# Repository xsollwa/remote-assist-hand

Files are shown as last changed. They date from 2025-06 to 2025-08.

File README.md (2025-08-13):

# remote-assist-hand
A robotic hand with pressure sensing and haptic feedback communication

**Created by:** Ruzanna Gaboyan and Philip Golczak  
**Date:** May 28, 2025  
**Demo:** https://youtu.be/ImFqXYvcVdE

## Overview
The **Remote Assist Hand** is a robotic arm with a gripping hand that is able to sense how much pressure it feels when gripping and holding objects. It uses a load cell to measure this force and sends that information to a computer through an ESP32 microcontroller. Unlike most robotic arms, **Remote Assist Hand** can *sense physical resistance and communicate it back* to the user, which helps them to know how hard the robot is gripping without directly touching anything. 

**Why we made it:** By this project we wanted to learn more about haptic feedback and *communicating the "feeling of touch"* while controlling robots. This is especially helpful for tasks that demand percision when it comes to pressure awareness: like when handling delicate objects.

## Features
- **Force sensing with load cell:** Senses how much pressure the hand feels when it grabs an object.
- **Real time feedback to computer**: ESP32 wirelessly sends data from the hand to a computer.
- **Remote control using computer**: The arm is designed to be operated remotely through a computer. 
- **Custom PCB and 3D design**: All parts including the base, casing and PCB are custom designed and printed

### Materials and Budget

| Part Number | Part Name | Description | Unit Price | Total Price |
| :--- | :---: | :---: | :---: | ---: |
| MP1 | ESP32 | [Wi-Fi Microprocessor][1] | $10 | $10 |
| B1 | Urgenex Lipo Battery (2x) | [Battery for Arm and Remote][2] | $27 | $27 |
| M1 | Digital Servo Motor (4x) | [Servos for Joints][3] | $45 | $45 |
| M2 | Stepper Motor | [Stepper for Base][4] | $13 | $13 |
| L1 | Load Cell | [Load Cell for Grasper][5] | $12 | $12 |
| A1 | Amplifier (4x) | [Amplifier for Load Cell][6] | $7 | $7 |
| D1 | Stepper Driver (3x) | [Driver for Stepper][7] | $8 | $8 |
| C1 | Hex Coupler 5mm (4x) | [Hex Coupler for Base][8] | $8 | $8 |
| T1 | Threaded Inserts 4mm (100x) | [Threaded Inserts for Arm][9] | $10 | $10 |
| BC1 | Buck Converter 4mm (2x) | [Buck Converter for 7.4-5v][10] | $8 | $8 |
| L1 | 5v Voltage Regulator | [Voltage Regulator for ESP32][11] | NA(Owned)  | NA(Owned) |
| PCB1 | Printed Circuit Board | [PCB for Electrical Components][12] | ~$10 | ~$10 |
| S1 | Boat Rocker Switch | [Power Switch][13] | $5 | $5 |
| TOT | Total (Excluding taxes, shipping and fees) | | | $163 |

[1]: https://www.amazon.com/HiLetgo-ESP-WROOM-32-Development-Microcontroller-Integrated/dp/B0718T232Z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

[2]: https://www.amazon.com/URGENEX-Battery-1800mAh-Rechargeable-Campatibal/dp/B0924MM61Z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

[3]: https://www.amazon.com/HOOYIJ-Digital-Waterproof-Crawler-Control/dp/B0CJ79WBZ8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

[4]: https://www.amazon.com/Stepper-Motor-Bipolar-64oz-Printer/dp/B00PNEQI7W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

[5]: https://www.amazon.com/uxcell-Weighing-Electronic-Balance-Sensor/dp/B07NS81RT6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

[6]: https://www.amazon.com/WWZMDiB-HX711-Amplifier-Displacement-Acceleration/dp/B0BLND4VF6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

[7]: https://www.amazon.com/WWZMDiB-Stepstick-Stepper-Printer-Suitable/dp/B0BFQZWT6R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

[8]: https://www.amazon.com/uxcell-Coupler-Coupling-Connector-Wheels/dp/B08M379TCT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

[9]: https://www.amazon.com/HANGLIFE-Heat-Set-Threaded-Printing-Components/dp/B0CS6XGMFD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

[10]: https://www.amazon.com/Maxmoral-Converter-Adjustable-Step-Down-Regulator/dp/B07MKQXNWG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

[11]: https://www.amazon.com/BOJACK-Regulator-Integrated-Circuits-Regulators/dp/B07VRS9HW4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

[12]: https://cart.jlcpcb.com/quote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

[13]:https://www.amazon.com/10PCS-Rocker-Switch-Rectangle-Black/dp/B094FWYWL5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

### Notes on Purchasing and Shipping
We want to purchase most of the parts from Amazon. We chose Amazon as our primary supplier because we have access to Amazon Prime, which has faster and free shipping. The free shipping makes the packs cheaper than the singular alternatives at other sources. Some components, like the voltage regulators, were only available in multi packs, so the unit price listed is price of the whole pack. Also, we plan to use some of the parts, like the battery and voltage regulators, for our next project, so their cost is shared across multiple builds!

## How it Works
1) Servo motors (controlled from a computer) move the arm and the gripper to **hold an object**,
2) The load cell inside the gripper **measures how much force** is being applied,
3) ESP32 **sends the data to a computer** in real time,
4) The computer **displays the pressure**, helping the user understand how hard the robot is gripping.

## Pictures 

**Overview Wiring Diagram**

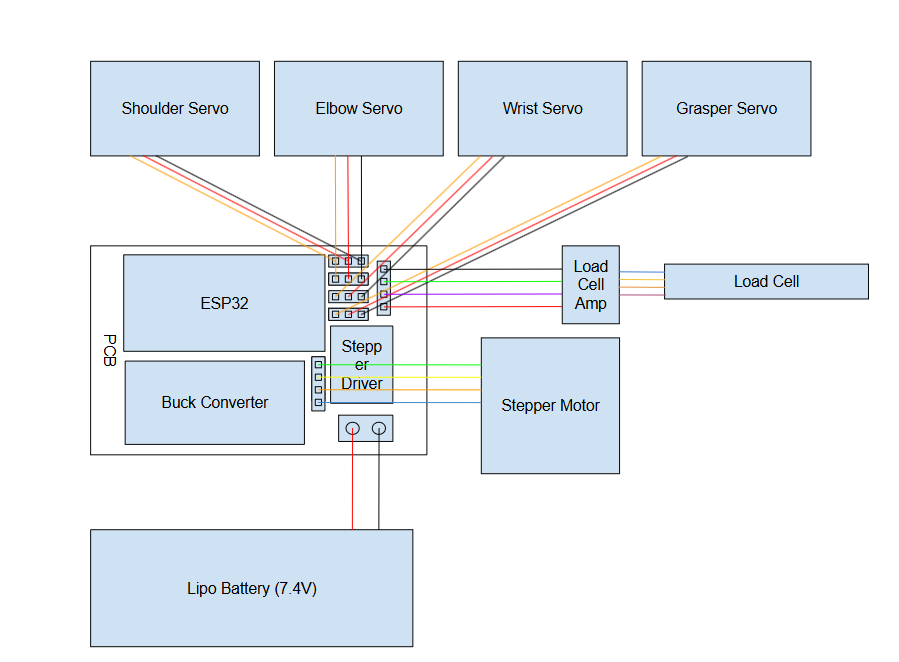
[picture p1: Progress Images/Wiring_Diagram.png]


**PCB**
Arm_Wiring_Final
PCB_Design

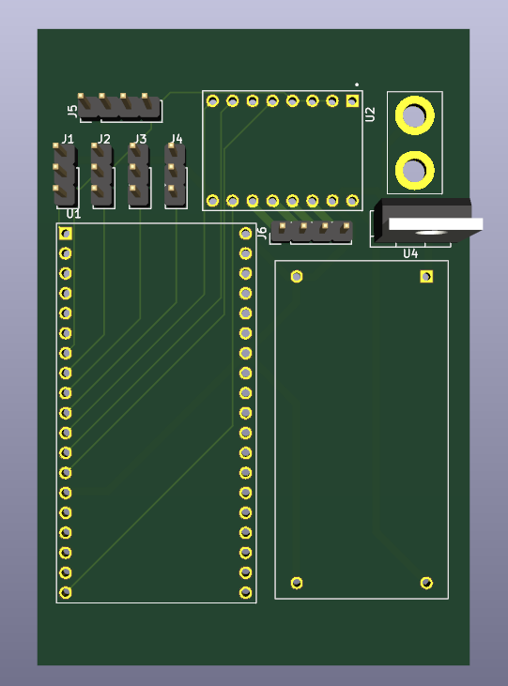
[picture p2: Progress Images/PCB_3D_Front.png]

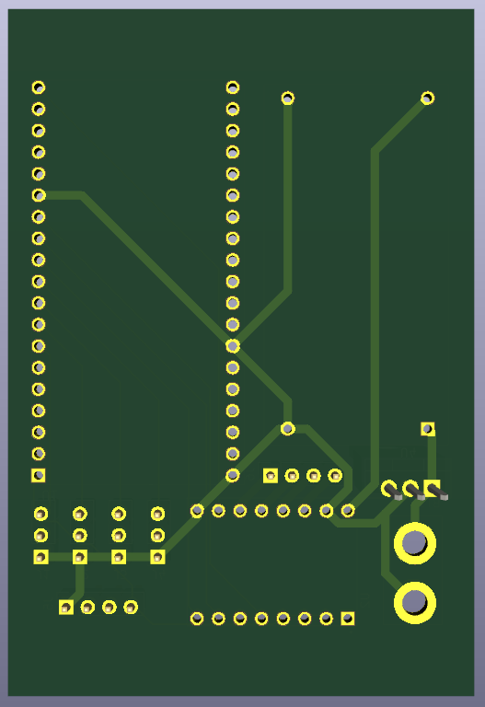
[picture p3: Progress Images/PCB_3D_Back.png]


**3D model**
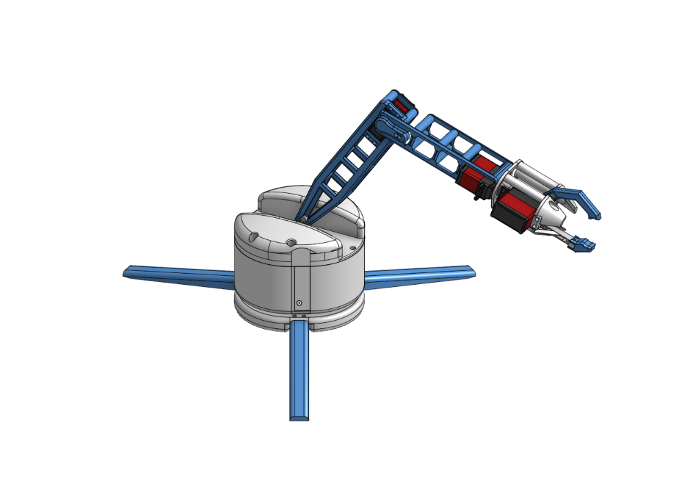
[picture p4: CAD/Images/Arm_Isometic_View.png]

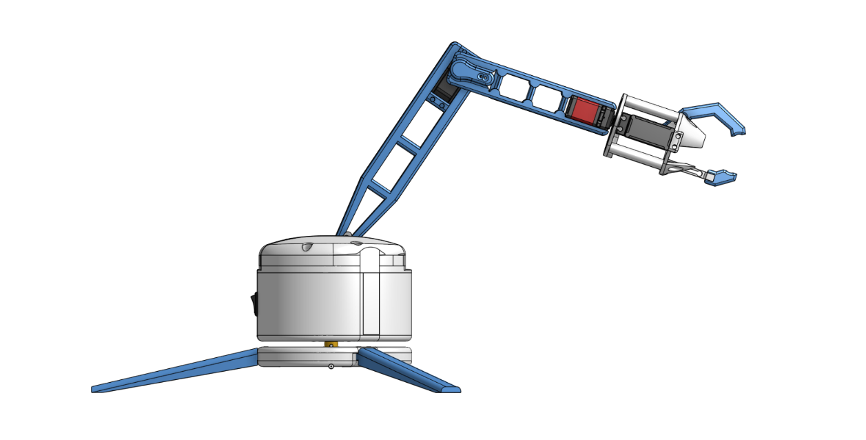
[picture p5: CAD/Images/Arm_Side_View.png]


**Build IRL**
Complete_Arm (1)

## Building Process
1) Brainstorming and sketching
2) PCB Design using KiCAD 
3) CAD Modeling using OnShape
4) Revision and Optimization
5) Assembly and testing

## Journal
Our full development journal can be found [here](./JOURNAL.md) (includes what we struggled with and what we learnt)

## Contact
For any questions or suggestions please reach out to us at *gaboyanruzanna@gmail.com* or *ph.golczak@gmail.com* .

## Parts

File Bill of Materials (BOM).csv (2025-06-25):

Part Number | Part Name | Description | Unit Price | Total Price
MP1 | ESP32 | Wi-Fi Microprocessor | $10 | $10
B1 | Urgenex Lipo Battery (2x) | Battery for Arm and Remote | $27 | $27
M1 | Digital Servo Motor (4x) | Servos for Joints | $45 | $45
M2 | Stepper Motor | Stepper for Base | $13 | $13
L1 | Load Cell | Load Cell for Grasper | $12 | $12
A1 | Amplifier (4x) | Amplifier for Load Cell | $7 | $7
D1 | Stepper Driver (3x) | Driver for Stepper | $8 | $8
C1 | Hex Coupler 5mm (4x) | Hex Coupler for Base | $8 | $8
T1 | Threaded Inserts 4mm (100x) | Threaded Inserts for Arm | $10 | $10
BC1 | Buck Converter 4mm (2x) | Buck Converter for 7.4-5v | $8 | $8
L1 | 5v Voltage Regulator | Voltage Regulator for ESP32 | NA(owned) | NA(owned)
PCB1 | Printed Circuit Board | PCB for Electrical Components | ~$10 | ~$10
S1 | Boat Rocker Switch | Power Switch | $5 | $5
Total (excluding taxes, shipping and fees): |  |  |  | $163

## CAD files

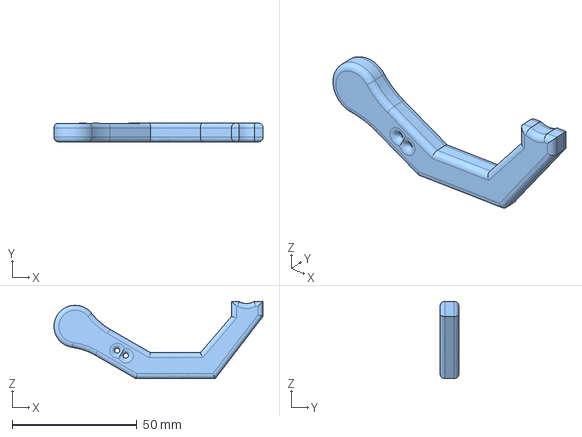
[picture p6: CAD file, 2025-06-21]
Production/Claw Top.step
83.9 x 7.50 x 31.0 mm

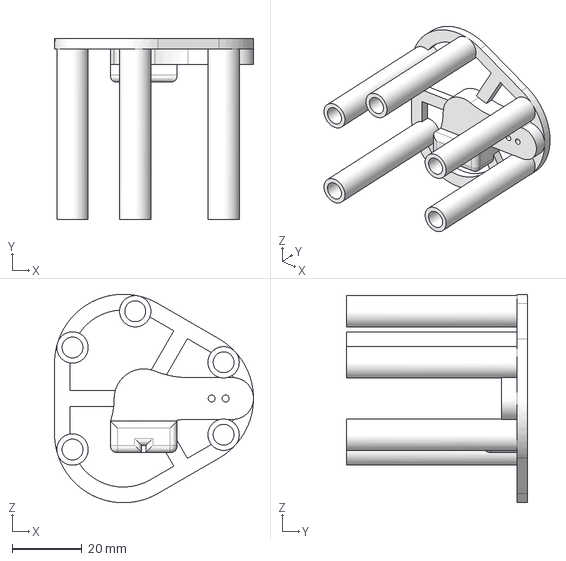
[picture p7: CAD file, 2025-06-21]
Production/Wrist Female.step
57.1 x 51.9 x 59.9 mm

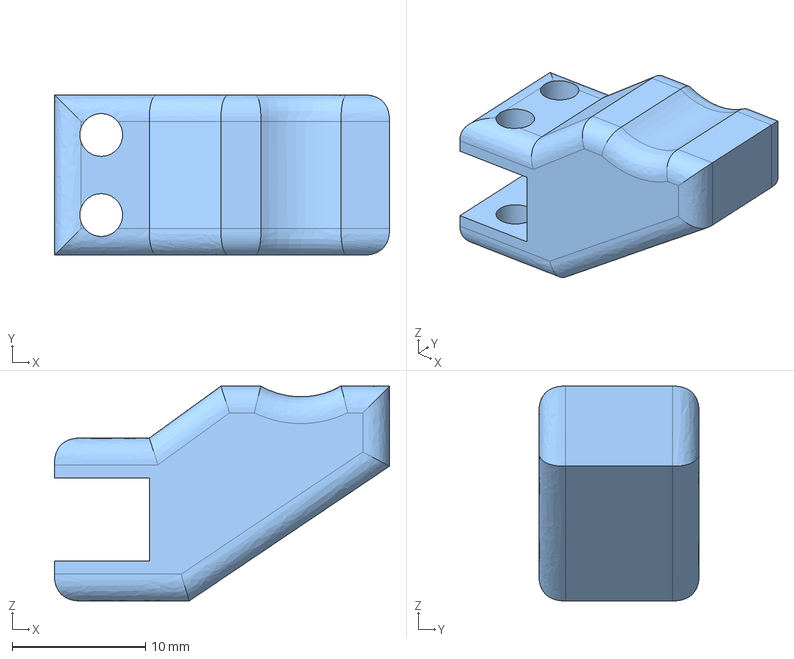
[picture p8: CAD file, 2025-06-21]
Production/Claw Bottom.step
25.1 x 12.0 x 16.1 mm

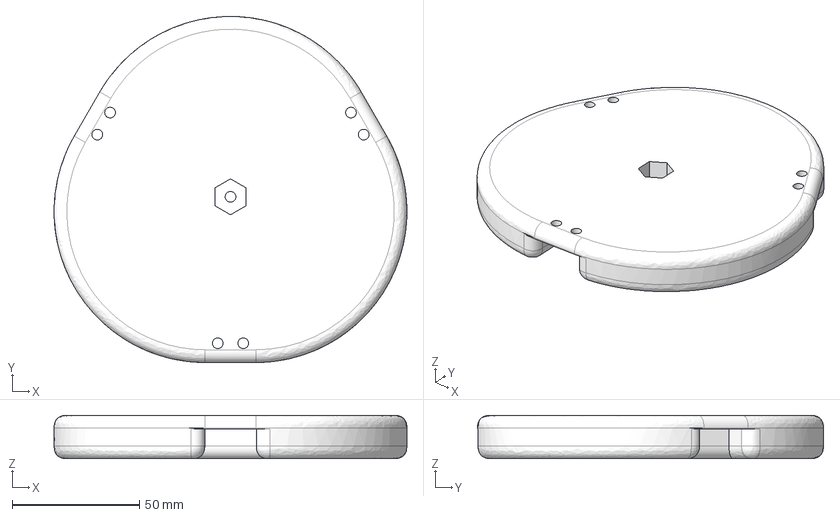
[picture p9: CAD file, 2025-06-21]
Production/Base Center.step
138.4 x 135.7 x 17.0 mm

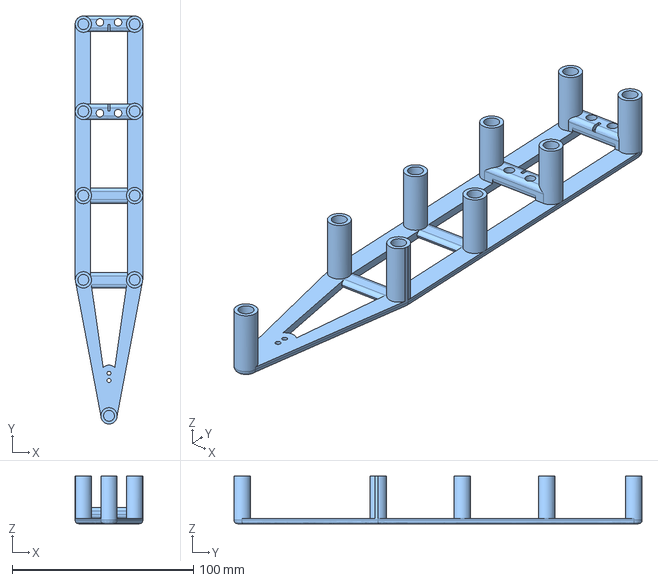
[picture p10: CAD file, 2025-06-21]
Production/Upper Arm Female.step
37.3 x 225.0 x 26.2 mm

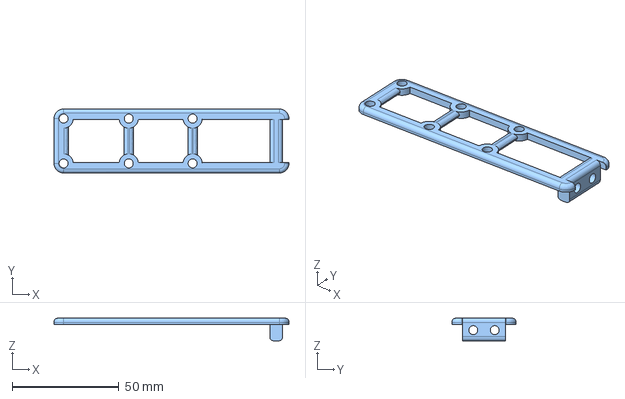
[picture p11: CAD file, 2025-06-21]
Production/Forearm Male.step
110.0 x 30.0 x 10.6 mm

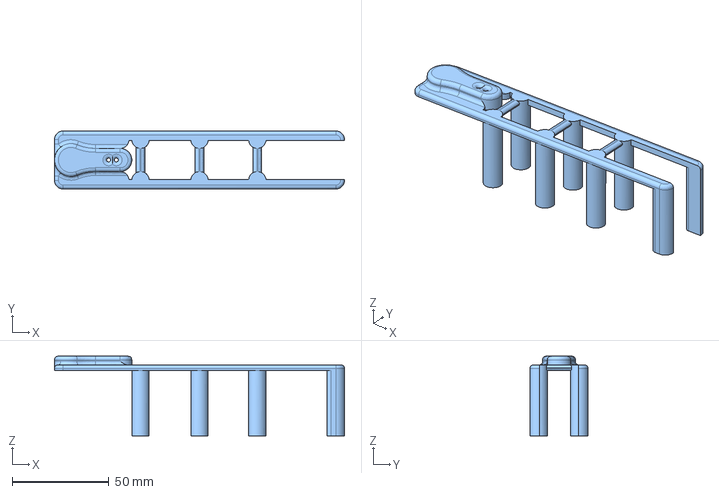
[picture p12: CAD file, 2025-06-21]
Production/Forearm Female.step
150.0 x 30.0 x 41.2 mm

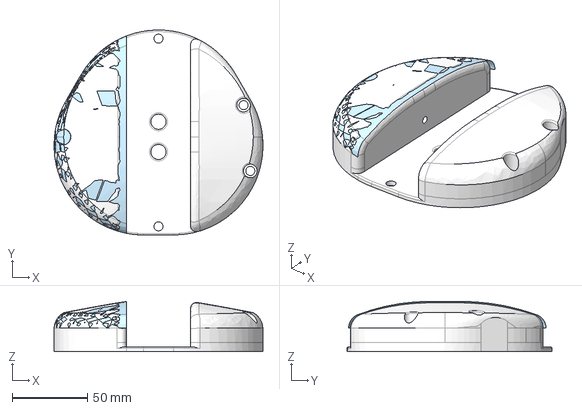
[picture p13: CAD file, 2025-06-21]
Production/Electronics Casing Lid.step
138.4 x 135.8 x 33.3 mm

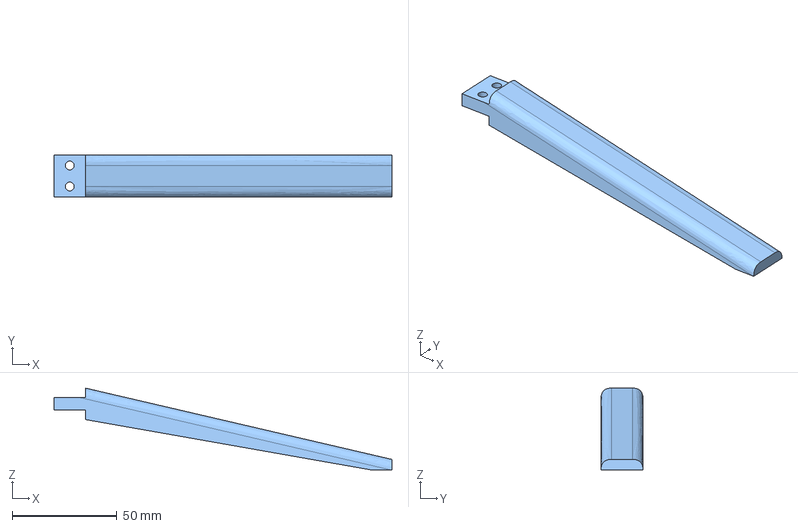
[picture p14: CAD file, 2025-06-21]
Production/Base Leg.step
161.1 x 20.0 x 39.0 mm

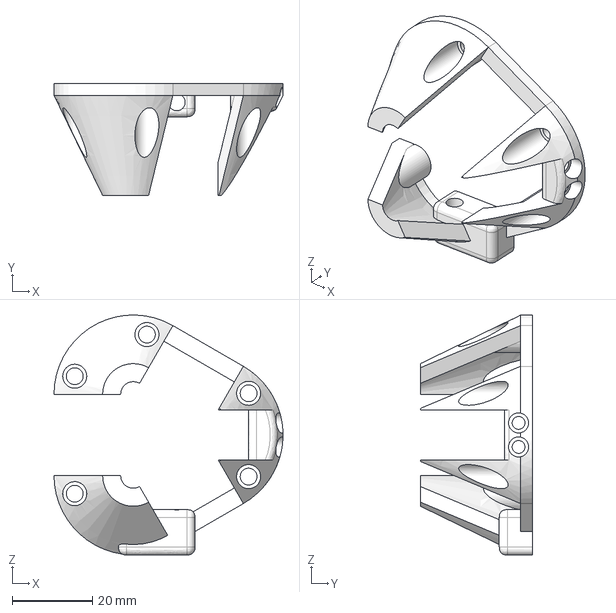
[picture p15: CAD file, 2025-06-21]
Production/Wrist Male.step
57.1 x 28.0 x 59.9 mm

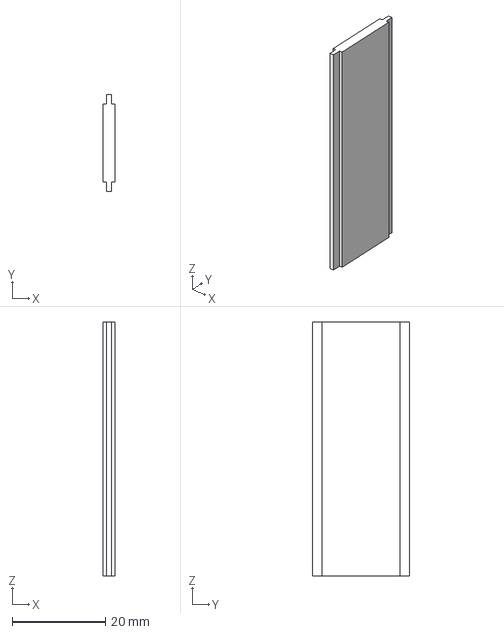
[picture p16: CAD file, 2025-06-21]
Production/Electronics Casing Panel.step
2.50 x 20.8 x 54.5 mm

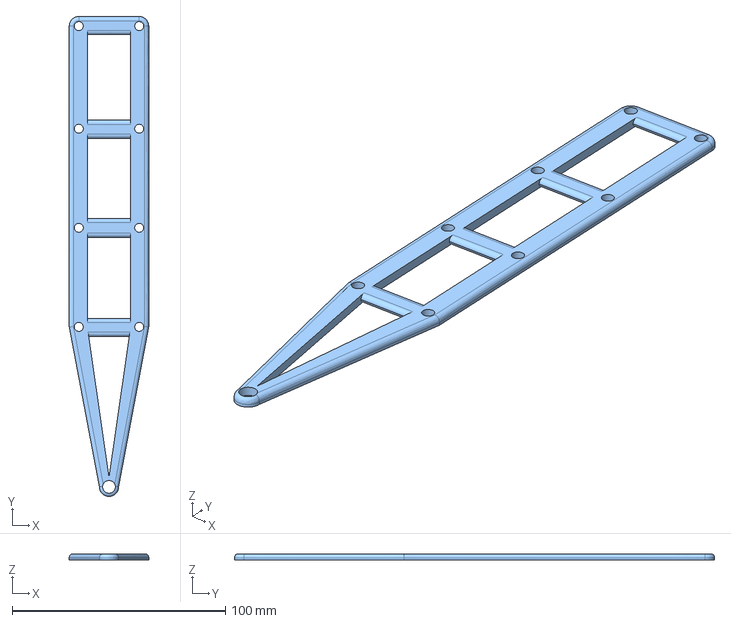
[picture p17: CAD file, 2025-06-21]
Production/Upper Arm Male.step
37.3 x 225.0 x 3.00 mm

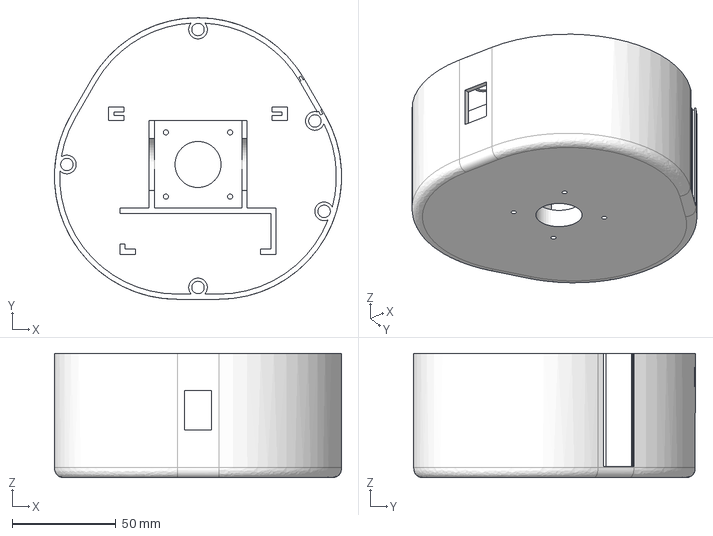
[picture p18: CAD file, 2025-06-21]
Production/Electronics Casing.step
138.4 x 135.8 x 60.0 mm

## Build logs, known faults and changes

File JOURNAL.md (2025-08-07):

---
Title: "Remote Assist Haptic Hand"
Authors: "Ruzanna Gaboyan and Philip Golczak"
Description: "For this project we are creating a robotic arm with a gripper hand which will have a pneumatic haptic feedback system"
Created_At: "2025-05-28"
---
# Total time spent (On design): 108 hours
**Ruzanna**: 30 hours

**Philip**: 78 hours

### May 27, 2025 - 2 hours

**What we did:**
- For our first work day on this project, we focused on brainstorming and research to get a clear picture of what we want to create. We discussed different project ideas that we had, some of which were focused on medical devices because of interest in biomedical engineering. After going through the pros, cons, and what the build process would look like for each concept, we decided to make a robotic hand with haptic feedback. The idea is that the hand could be useful in situations like small-scale surgeries or remote object handling where you need a sense of "touch" or grip resistance.
  
- One challenge we had was figuring out how to successfully achieve a functional haptic feedback system. After doing some research, we decided on trying to implement haptic feedback based on air pressure. The concept seems simple and effective. we’ll use a small tube with that you squeeze with your hand. The more you squeeze it, the more pressure it senses, and the robotic hand will close proportionally to that pressure. We want it tp work both ways. When the robotic hand feels resistance (like from gripping an object), it pushes air back into the tube, which increases the pressure and makes it physically harder to squeeze.
  
- To make the use of the arm easier, we decided to make it remotely controllable, and we are planning to use a joystick or remote control for that (We will make a joystick/controll-pad for robotic hands with XYR controls, airbulb and haptic feedback system for our second Highway project!). Here is one useful article that we read to get an insight on how to build remotely controllable robot arms:
https://www.instructables.com/remote-controlled-robotic-arm/

- Here is a useful video that we watched which was also about building robotic arms:
https://youtu.be/5toNqaGsGYs?si=Z9oADLPzUGIuOL0S
(The robotic arm in this video is pretty big but ours will be smaller) 

### June 3, 2025 - 4 hours

**What we did:**
- We set up Visual Studio Code Git extension and cloned the project repository to our computers. We did this to make the workflow smoother since we plan to write the C code for our Arduinos in Visual Studio Code.

- We chose the mechanical parts such as the stepper and servo motors to drive the arm based on power requirements. We also chose our microcontroller allowing for Wi-Fi connectivity using an Arduino model for familiarity. Added these components to the Material and Budget file listing their prices and linking to possible vendors.

### June 4, 2025 - 1 hours

**What we did:**
-  We met to brainstorm and discuss the physical design of the robotic arm, more specifically the size of the robot, and how the CAD and PCB would look like. We came up with a design that would be slightly smaller than real human arm because of the strength and size of the motors we are planning to use.
  
-  We began sketching out the CAD design on paper, dimensioning out the arms and making sure our servos can support the torque provided by the weight of the arm. This should allow for easier CADing in the future and smooth operation of the arm.

### June 5, 2025 - 2 hours

**What we did:**
- We continued to add to the Materials and Budget list allowing us to shape out the details of the claw itself as we found components needed for the pressure feedback such as a load cell and amplifier. Now having the components needed for the arm we plan on moving onto finding the components for the controller and fully CADing out the arm.
  
- We also had the meeting with Alex to discuss our project and progress. He suggested using an ESP32 microcontroller instead of the Arduino Nano, as it may be more cost-effective and have better WiFi capabilities, so that is what we will move forward with.

### June 6, 2025 - 2 hours

**What we did**

*Ruzanna*
- Today I created the first detailed drawing of our robotic arm design. The goal was to visualise how each component would physically fit together; it includes labeling of all of the parts that will go into building the arm (servo motors M1-M4, stepper motor Mst, gripper, load cell L1, amplifier A1, ESP32, MPX5010DP with its tube, and LiPo battery). Here is the first sketch!


- After sharing the design with Philip we discussed how feasible it is and how the pressure feedback system should work. Originally I drew in MPX5010DP with a tube to register pressure, but we ended up coming up with a better way. We agreed to measure haptic feedback electrically through a load cell L1 which measures the amount of bending force applied by the gripper. So, I revised my drawing to its second version by removing the air pressure tube with the MPX5010DP sensor , and included a pressure display on the arm to show live force readings using the load cell. Here is the revised version of the sketch:


### June 11, 2025 - 4 hours

**What we did**

*Philip*
- Today, I worked on fleshing out many of the ideas Ruzanna and I had previously discussed by CADing out some of the significant parts of the arm. I started by importing models of the stepper and servo motors we would be using, then CADing out the load cell as well as the Hex adapter, which would allow for 360-degree rotation. Next, I designed the stationary base, as well as the component for storing various electronics, including the PCB and stepper motor. These parts are denoted by the color blue, as we will 3D print them to construct the arm.

- Tomorrow, I plan to create the PCB design for the arm, which will enable me to scale the arm more effectively and continue refining the current parts that I will be printing. I am attaching images of my CAD progress thus far.
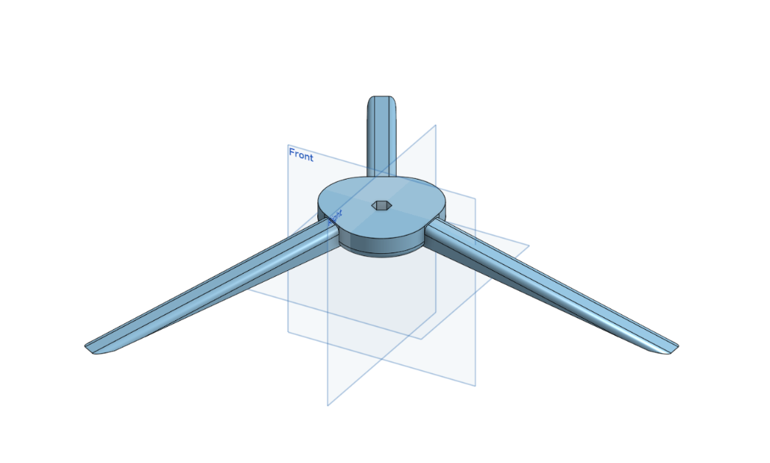
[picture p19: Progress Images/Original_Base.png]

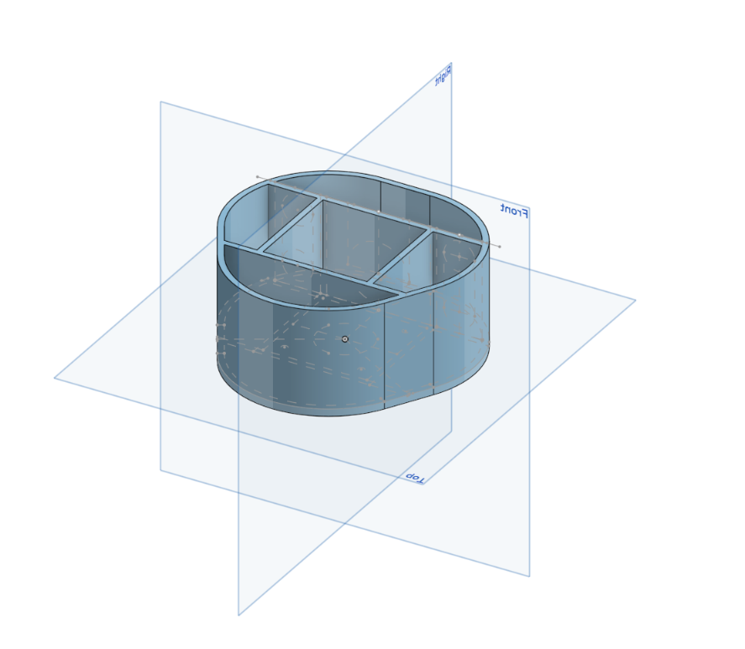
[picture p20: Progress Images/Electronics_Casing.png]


- The top image shows the stationary base, while the bottom represents the electronics casing, which will sit on top of it, supported by the hex adapter and stepper motor shaft.

- I also conitnued to form on the BOM and will be adding these updates tomorrow as I finish CADing.

### June 12, 2025 - 7 hours

**What we did**

*Philip*
- Today, I continued working on the CAD, mainly changing the base so that the legs can be printed separately from the base center. This change was to allow for the printing of these parts, as the combined model would not have fit on my 3D printer otherwise. Additionally, this will enable me to scale them to larger sizes if needed. Below is a picture of the new parts.
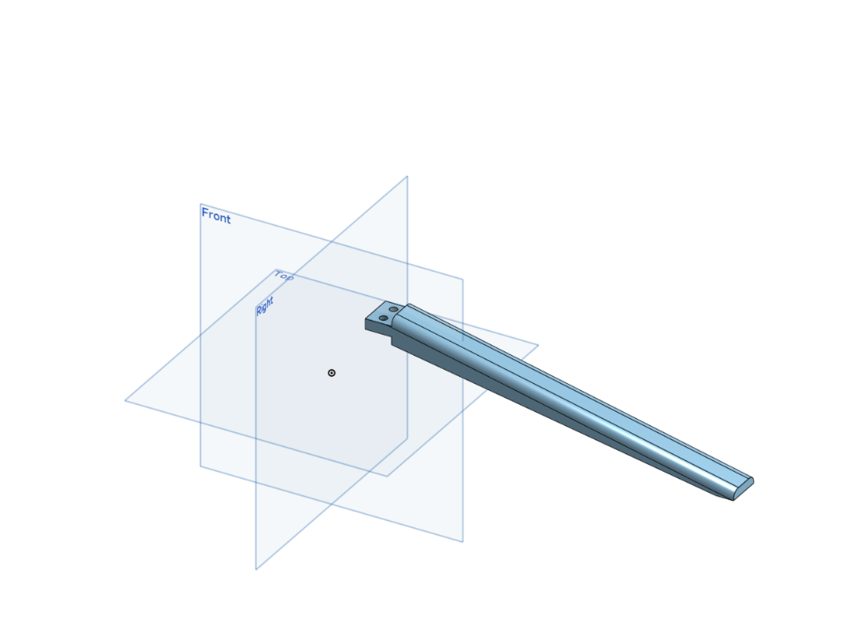
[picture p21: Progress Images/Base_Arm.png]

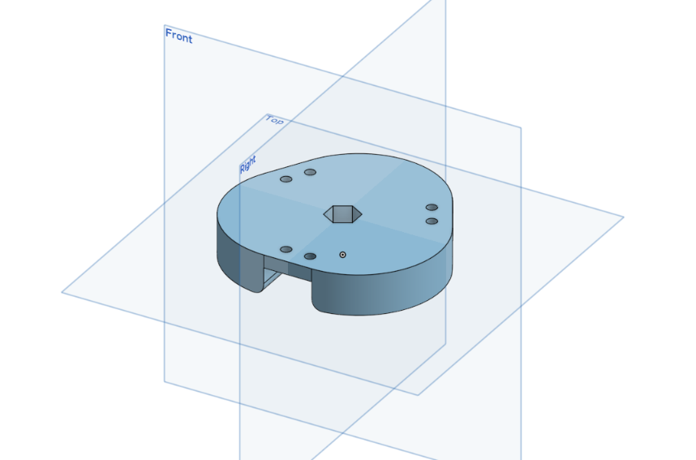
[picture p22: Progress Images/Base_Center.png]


- The bulk of my work today was spent on KiCAD. Today was my first time using the software. Thus, I spent a considerable amount of time learning how to use it. However, I was able to create my wiring diagram and start my actual PCB design. Below is a picture of my complete wiring diagram.
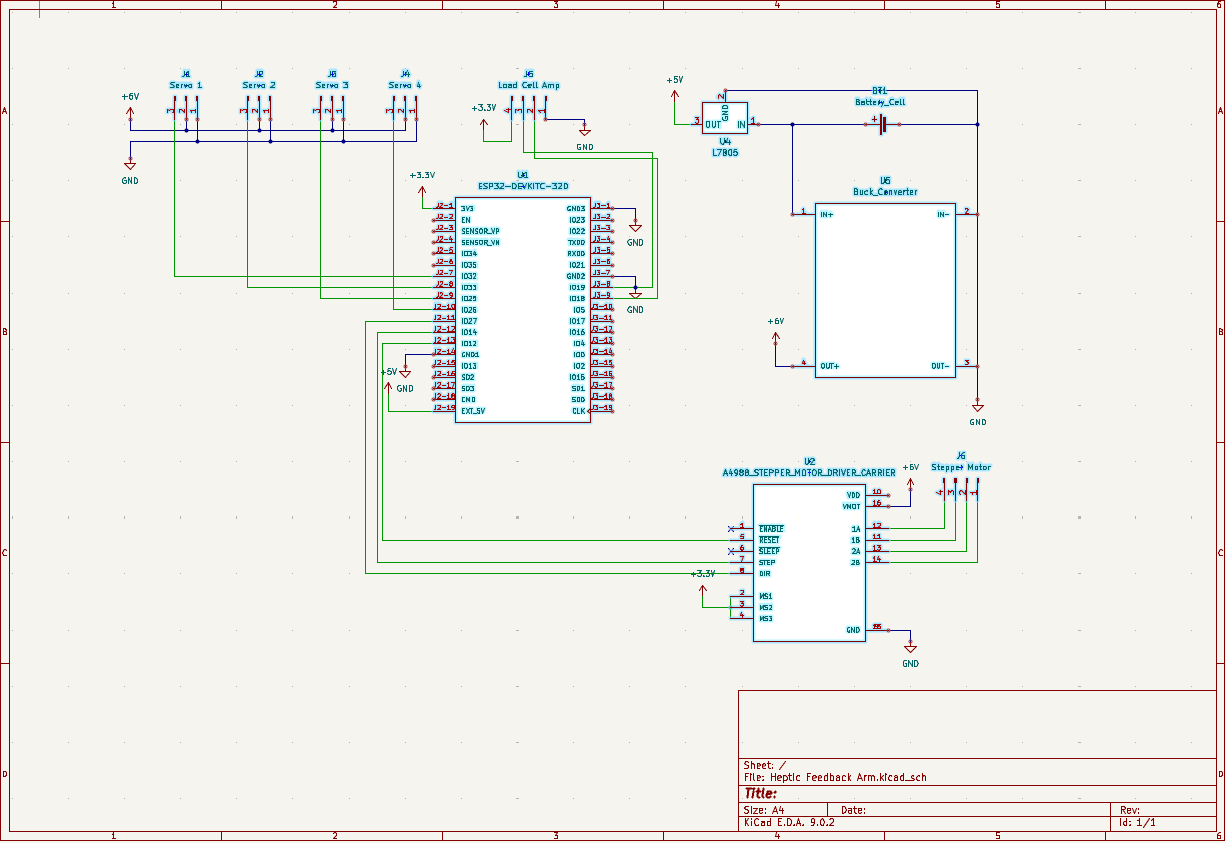
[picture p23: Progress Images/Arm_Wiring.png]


### June 13, 2025 - 5 hours

**What we did**

*Philip*
- I continued to refine my wiring diagram in KiCAD. I was able to complete both tasks, fully optimizing the PCB design for the smallest size while ensuring all the proper electrical connections were made. A part of this design process that took me a while to figure out was creating different nets, which I used to make the connections between my battery and other high-power connections thicker and make those connections as short as possible to reduce voltage drop. Below are pictures of both my complete wiring diagram and PCB design.
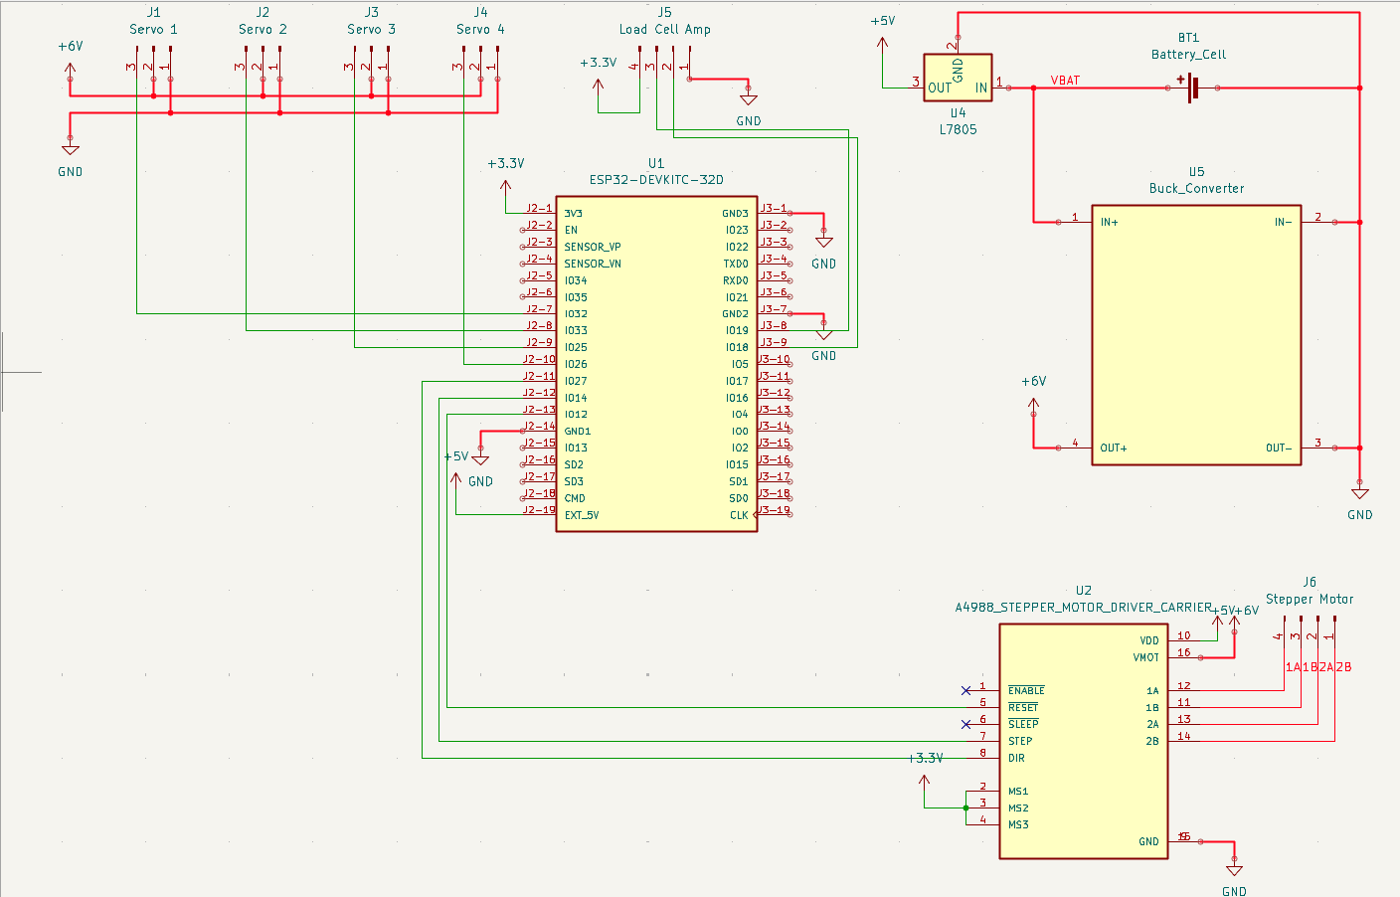
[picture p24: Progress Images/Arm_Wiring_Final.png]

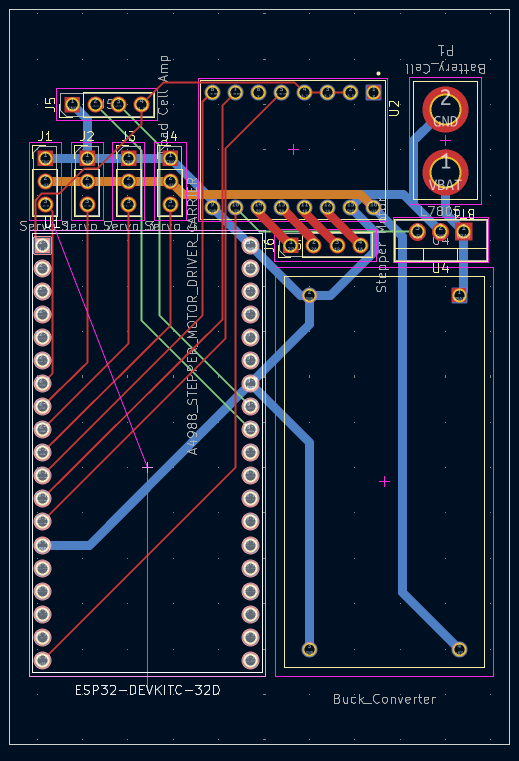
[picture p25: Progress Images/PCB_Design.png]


- Next, I imported the 3D model of my PCB into OnShape. I refined my Electrical Casing Design, as well as the base, to allow for the proper amount of space to fit all the electrical components. This resizing included the base center to accommodate the new, enlarged size. Below is an image of the new casing.
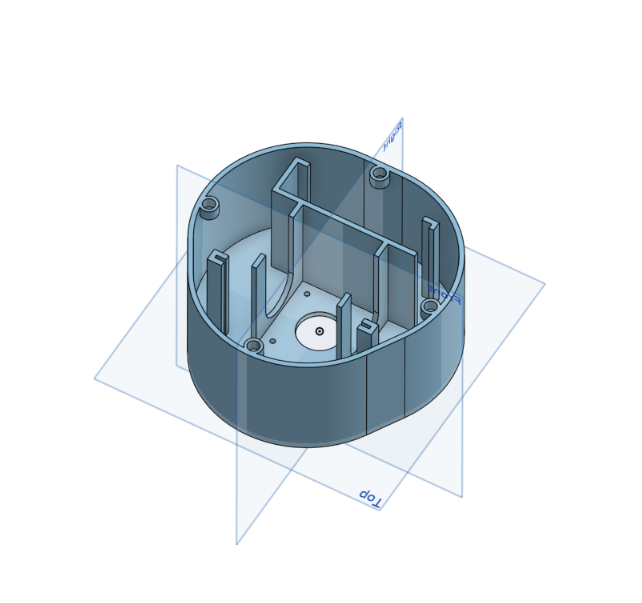
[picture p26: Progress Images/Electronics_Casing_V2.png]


### June 14, 2025 - 5 hours

**What we did**

*Philip*
- I continued working on the Electronics Case, notably adding a panel to access the ESP32 while the lid was screwed on, allowing for easy programming. Additionally, I added a hole for a switch that will enable me to turn off the power from outside the case, even when the lid is screwed on, which protects my programming device from high voltage. Next, I added the lid to hold both the first servo motor and allow for wiring to exit the arm. It also features an additional hole for a screw and nut, providing extra support for the arm. Below are pictures of the new case, panel, and lid.
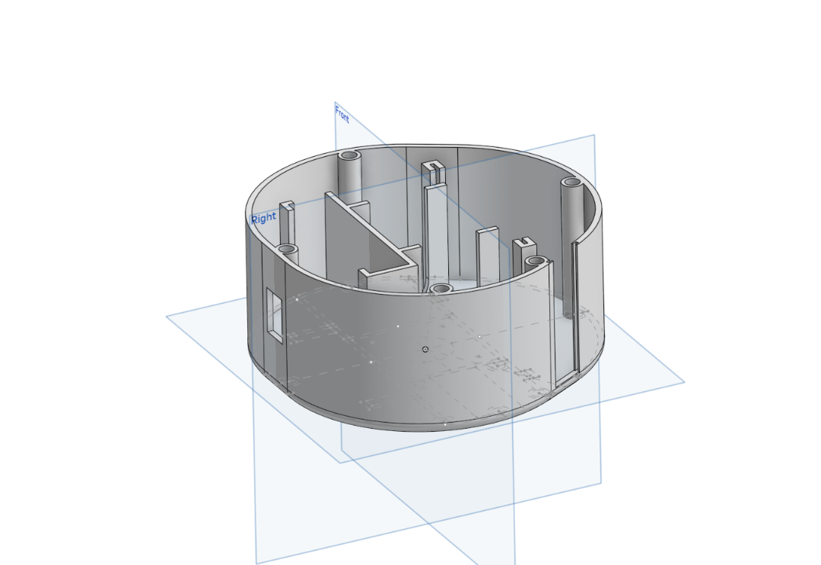
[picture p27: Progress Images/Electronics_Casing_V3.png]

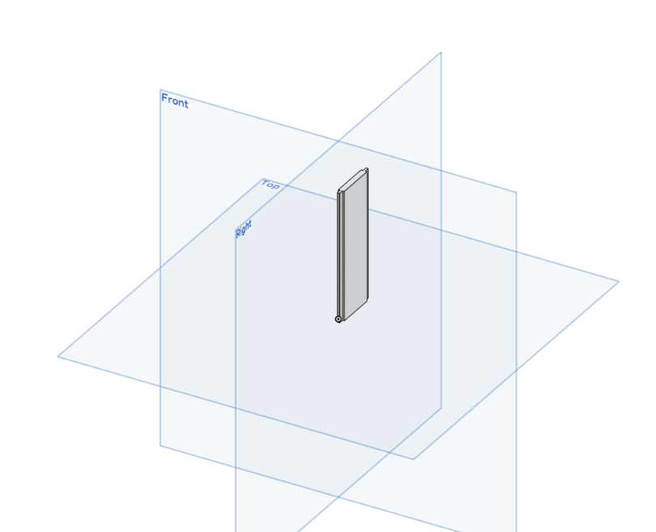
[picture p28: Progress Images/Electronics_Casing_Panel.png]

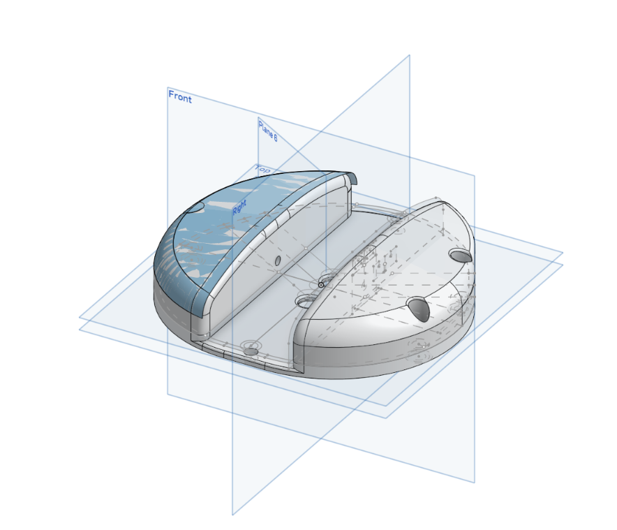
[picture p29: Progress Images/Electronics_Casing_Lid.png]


### June 15, 2025 - 4 hours

**What we did**

*Ruzanna*
- Today I completed the [README.md](./README.md) file of this project. In the README I covered the overview of the project, its key features, components, work process, build process and included links to important files such as the MATERIALS-AND-BUDGET.md and JOURNAL.md.
  
- After, I visited the highway website to make sure the project meets submission requirements. I had to make some changes in the README and ensured that the project repository looks organised.

*Philip*
- I shifted my attention to the upper arm area of the robot, CADing out both the male and female halves to ensure the servo motor fit snugly within them. These halves will be held together by M4 screws and threaded inserts and attached to the servo motor. Below are pictures of both of these parts.
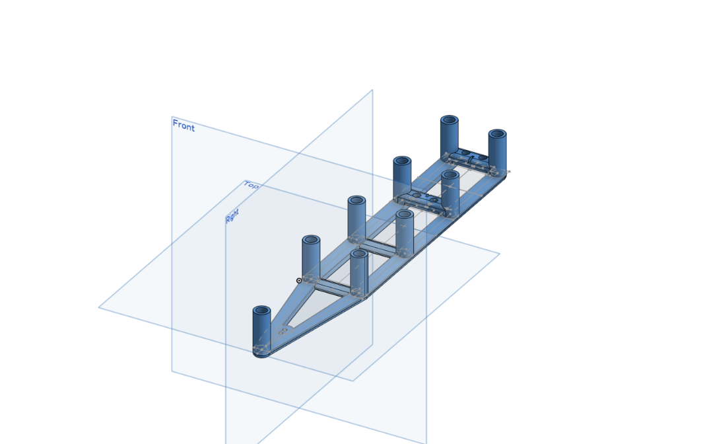
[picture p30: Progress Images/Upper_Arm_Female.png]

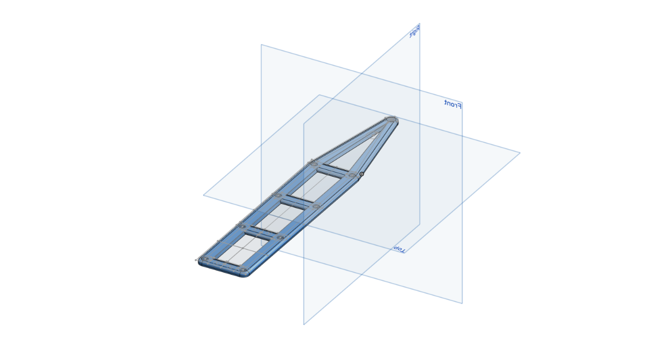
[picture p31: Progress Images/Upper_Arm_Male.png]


### June 16, 2025 - 2 hours

**What we did**

*Philip*
- Today, I moved on to what will be the forearm of the robot, once again CADing both the male and female components and finding a suitable location for the servo motor that will power the wrist joint while ensuring the design has sufficient space for any necessary wiring. Below are images of the two parts.
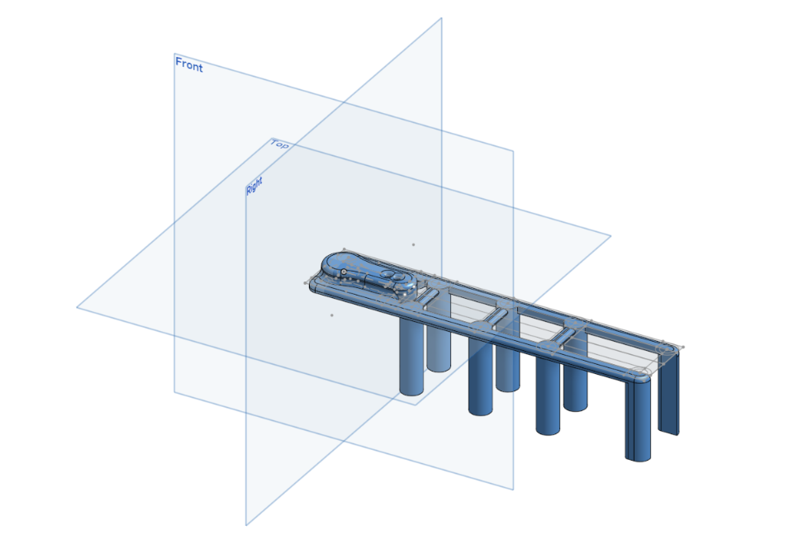
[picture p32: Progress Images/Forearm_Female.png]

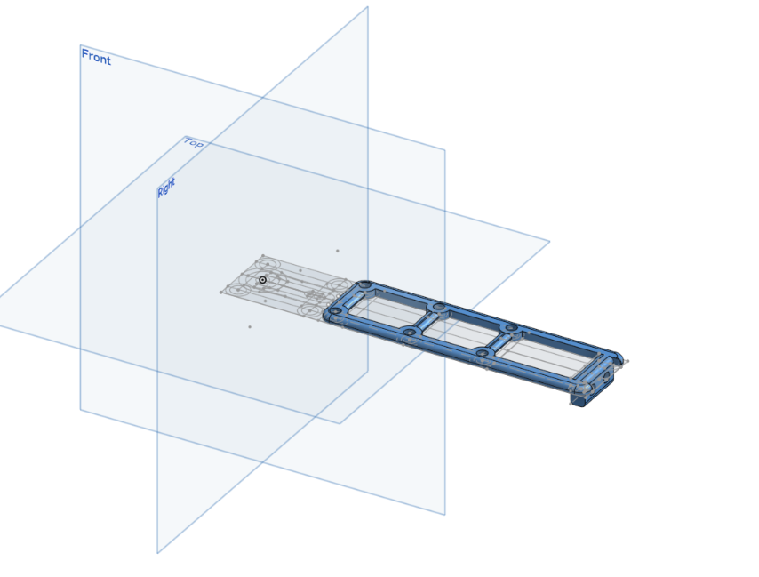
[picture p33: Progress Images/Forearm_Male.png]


### June 18, 2025 - 5 hours

**What we did**

*Philip*
- Today, I designed the wrist joint in CAD, which will hold the 4th and final stepper motor for the claw. This design should not have taken me as long as it did. Still, I was determined not only to ensure the stepper fit well but also to make the design appear polished and sleek while maintaining proper tolerances on these parts and, once again, allowing for room for any wiring. I also made sure to consider how the parts would be installed so that the construction would be easy. Below are images of the two parts of the wrist for both females and males.
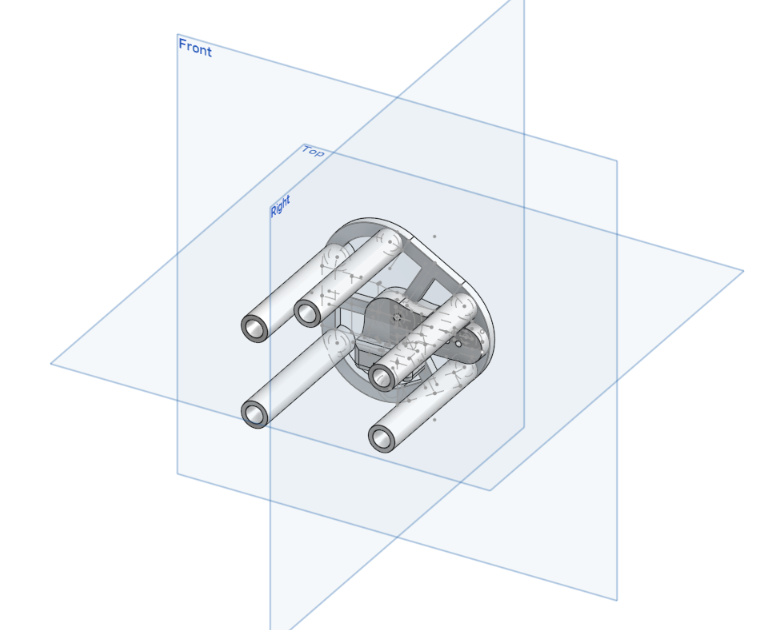
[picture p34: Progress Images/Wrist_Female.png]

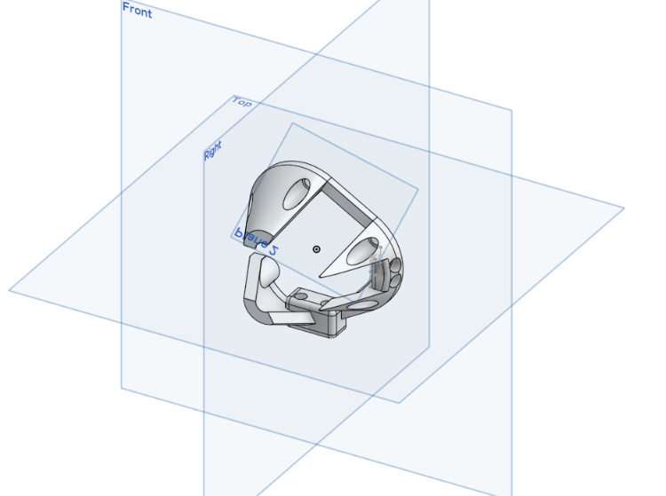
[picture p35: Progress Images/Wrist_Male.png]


### June 20, 2025 - 5 hours

**What we did**

*Philip*
- Today was my final day of designing the CAD model; I finished completing the models of the upper and lower claws and finally assembled all the pieces into one. I learned a lot about effective ways to create CAD models of very different shapes, as well as what it means to design a project in CAD from start to finish. While I enjoyed this process, after pouring so many hours into it, I am glad to be done. Below are images of both pieces of the claw as well as the whole assembly.
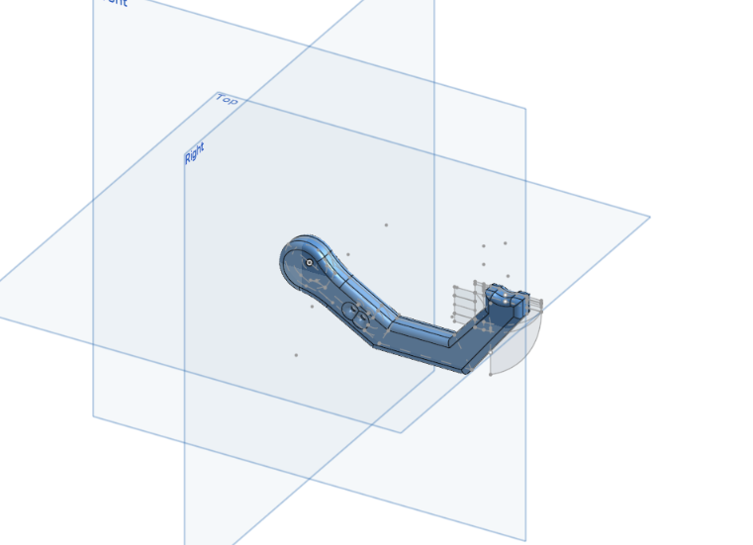
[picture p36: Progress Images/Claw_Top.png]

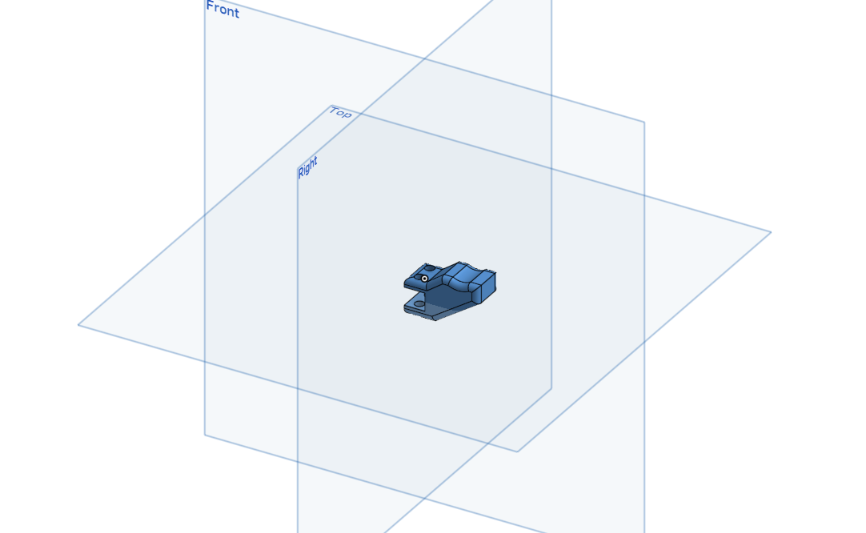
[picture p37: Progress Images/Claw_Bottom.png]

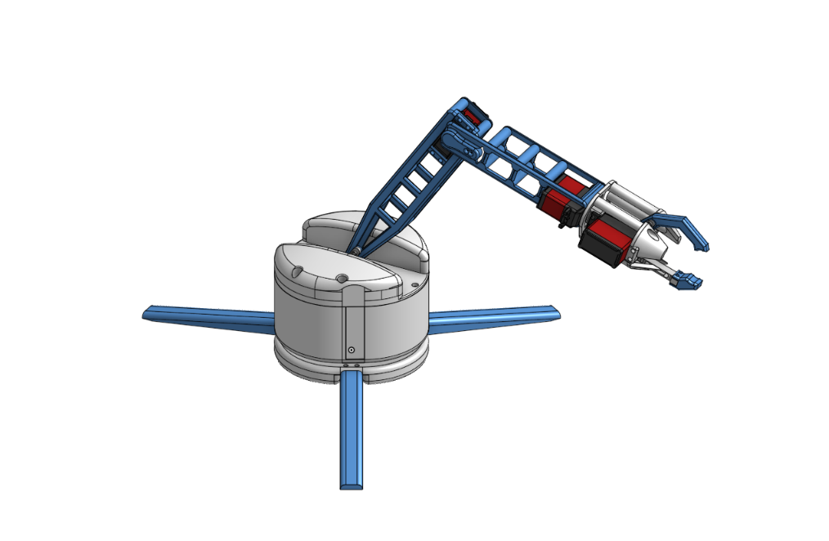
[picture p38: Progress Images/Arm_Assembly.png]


### June 21, 2025 - 1 hour

**What we did**

*Ruzanna*
- Today I organised the folders of the repository, converted BOM to its necessary format, and double-triple checked meeting all the highway submission requirements, making the necessary tweaks!

### June 24, 2025 - 8 hours

**What we did**

*Philip*
- Today I designed and implemented the complete web-based control interface for the robotic hand. First, I wrote the HTML, CSS, and JavaScript UI that the ESP32 will serve to a browser, adding buttons for each joint and a live force readout. Next, I encapsulated that interface in a main_page.h header using PROGMEM so the ESP32 can efficiently host it. Finally, I developed the Arduino sketch: it connects to Wi-Fi, starts HTTP and WebSocket servers, parses JSON commands from the browser to drive the A4988 stepper and four servos, and periodically reads the HX711 amplifier to convert the raw load-cell output into newtons and stream it back to the client in real time. Below is a pricture of the HTML webpage.
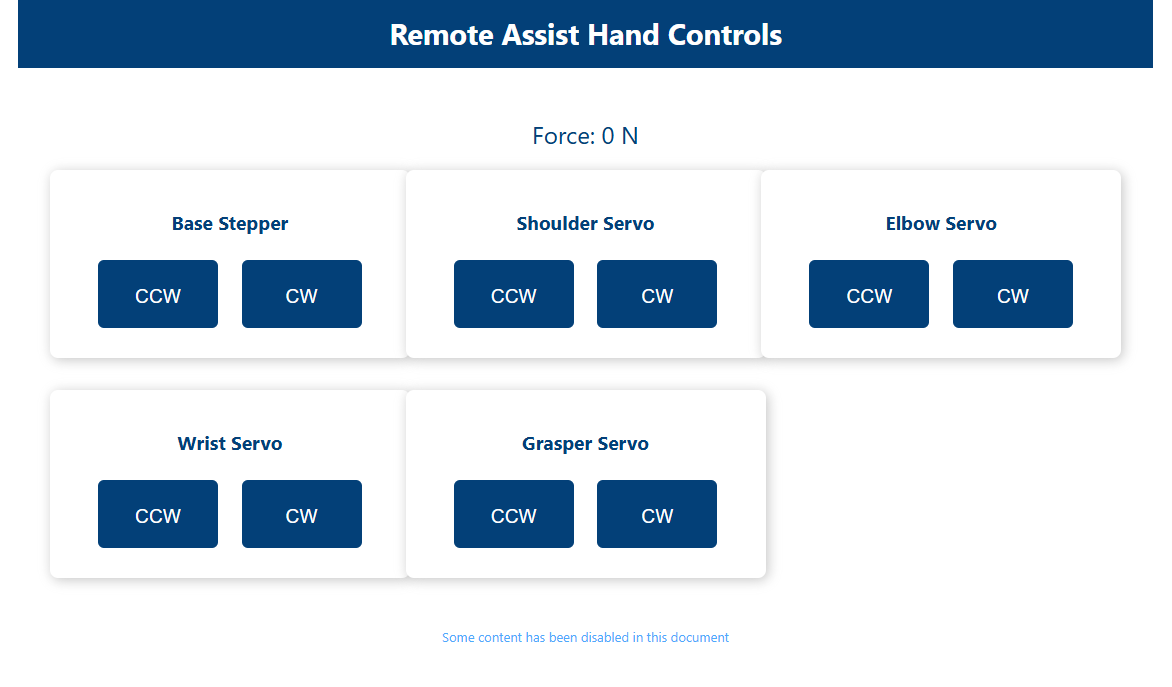
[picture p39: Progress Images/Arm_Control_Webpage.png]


- I completed the overview wiring diagram, which shows how all the electrical components, except those inside the PCB whose wiring is detailed in how the schematic, will be connected. Most notably, it shows how the four wires from the load cell will connect to the amplifier, which was previously not shown in the schematic.


### July 5, 2025 - 10 hours

**What we did**

*Philip*
- After our project was approved and the funding was secured, I ordered all the required components for the build. While waiting for the shipments to arrive, I 3D-printed all the structural parts for the arm. Once the components arrived, I assembled the robotic arm, including precise alignment of the joints, mounting the servos, and integrating the load-bearing sections. I also soldered and connected all electronic components to the custom PCB, ensuring proper routing and cable management. Below is a picture of the fully assembled arm:
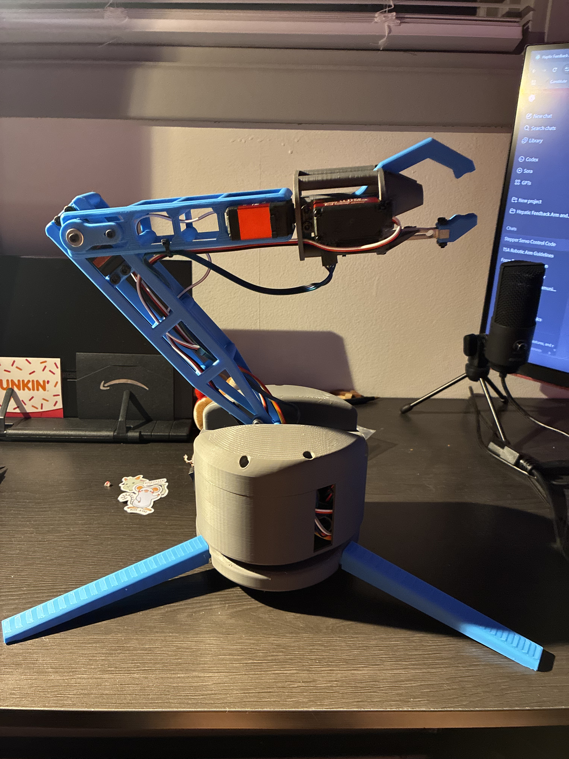
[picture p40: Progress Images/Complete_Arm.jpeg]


### July 10, 2025 - 3 hours

*Ruzanna*
- I worked on soldering electronics today! It was a bit tricky at first, but I’m getting better at making clean connections and figuring out where everything goes. I’m starting to feel more comfortable using the soldering tools and fixing little mistakes when something doesn’t connect right. This was my third soldering attempt!

### July 11, 2025 - 4 hours

*Ruzanna*
- While we were waiting for Undercity to Kick-off, we decided to continue working on assembling the arm at GithubHQ! It was a fun and productive way to use the time and we really appreciated the peers who stopped by to check out our project and offer help. Their interest meant a lot and even helped us catch a couple of things we hadn’t noticed.
  
- After putting most of the arm together, we started testing and debugging our code for the arm, which was one of the most challenging phases of getting the arm to work. Even though the hardware was mostly in place, the arm didn’t move the way we expected at first. We had to go through the code, check how each motor was responding, and fix issues with timing and control signals. It took a lot of trial and error...





### August 5, 2025 - 8 hours

**What we did**

*Philip*
- I spent the day updating and refining the robotic arm’s control code. Throughout July, I had been intermittently working on improving the arm’s motion, but today I implemented several new features and focused on smoothing out the movements. I also added functionality that allows the arm to remember its last position and automatically return to it upon power-up, improving both usability and safety.

### August 6, 2025 - 8 hours

**What we did**

*Philip*
- Today I continued improving the control code, primarily focusing on calibrating the load cell to ensure accurate and stable readings. Unfortunately, during testing, one of the safety constraints on the grasper failed, causing it to over-rotate and break the load cell. I temporarily replaced it with a 3D-printed substitute (pictured below along with the damaged load cell).
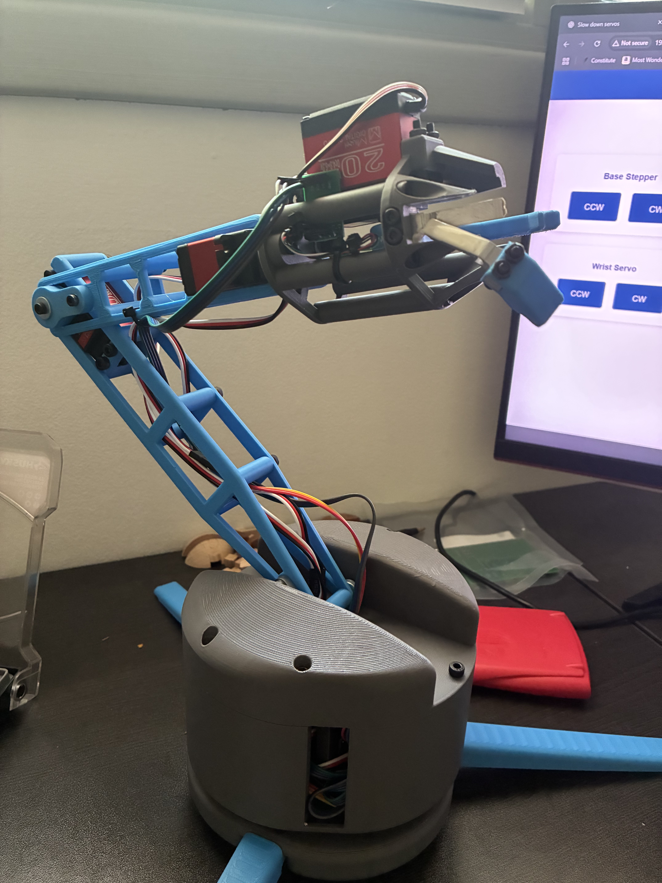
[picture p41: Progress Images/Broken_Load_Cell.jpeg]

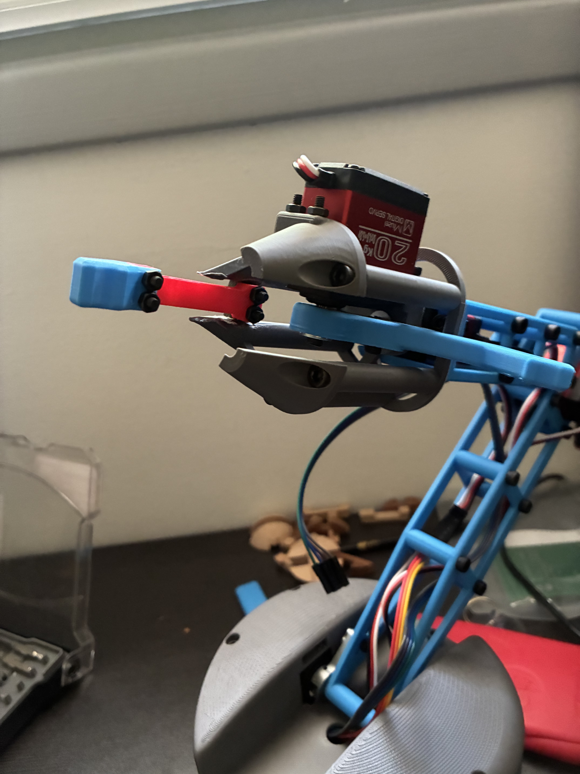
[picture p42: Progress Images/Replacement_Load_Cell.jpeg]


- Despite the setback, I was able to correct the motion issues, complete testing, and successfully record a demonstration video, which is linked below.

https://youtu.be/ImFqXYvcVdE

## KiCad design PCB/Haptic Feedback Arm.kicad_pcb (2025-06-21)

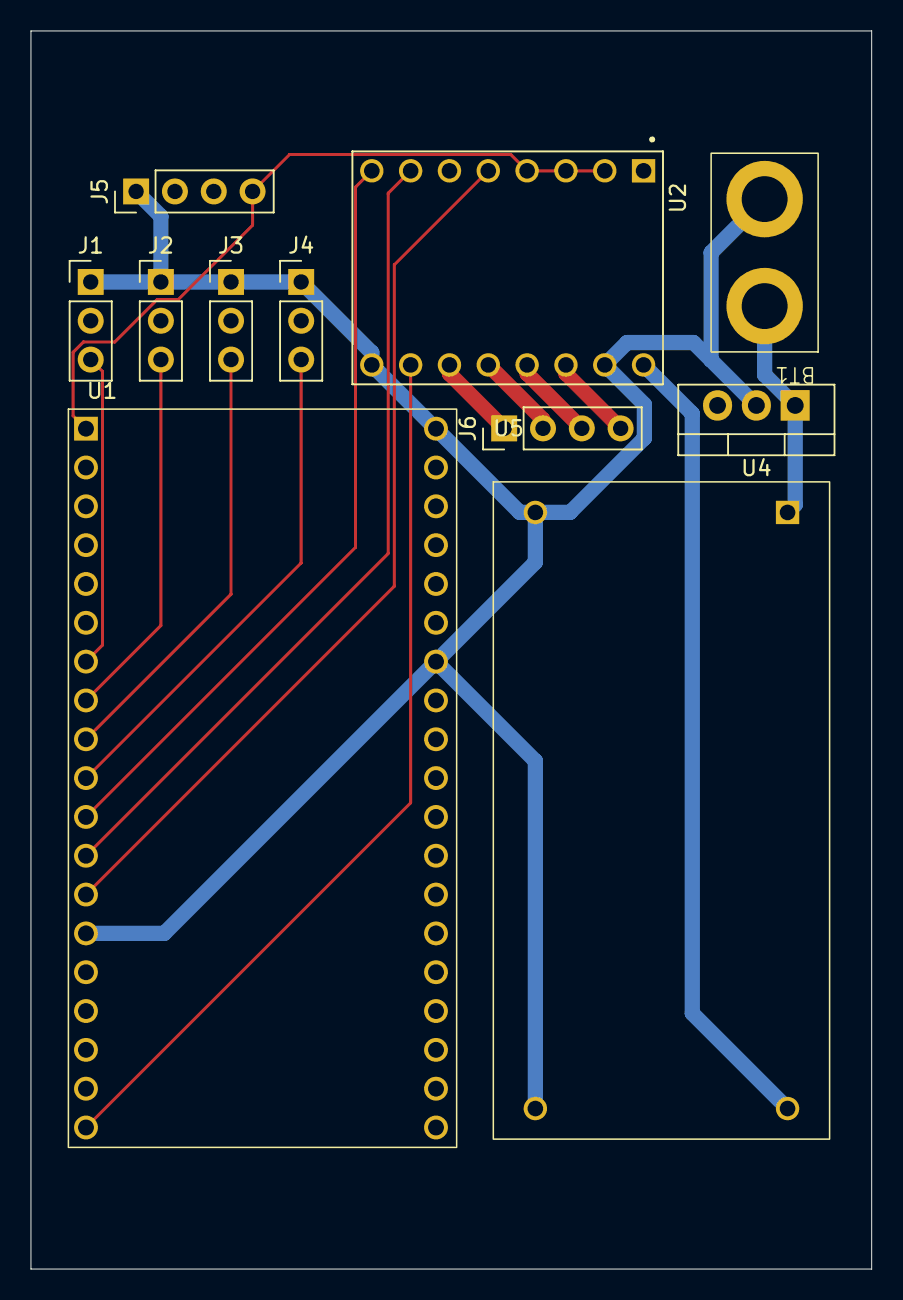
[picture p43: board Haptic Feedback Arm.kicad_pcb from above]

Board: 4 copper layers, 55.0 x 81.0 mm, 11 parts (0 on the bottom side), 18 nets.

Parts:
BT1: Battery_Cell; Lipo Battery T Plug
J1: Servo 1; PinHeader_1x03_P2.54mm_Vertical
J2: Servo 2; PinHeader_1x03_P2.54mm_Vertical
J3: Servo 3; PinHeader_1x03_P2.54mm_Vertical
J4: Servo 4; PinHeader_1x03_P2.54mm_Vertical
J5: Load Cell Amp; PinHeader_1x04_P2.54mm_Vertical
J6: Stepper Motor; PinHeader_1x04_P2.54mm_Vertical
U1: ESP32-DEVKITC-32D; ESP32_1
U2: A4988_STEPPER_MOTOR_DRIVER_CARRIER; MODULE_A4988_STEPPER_MOTOR_DRIVER_CARRIER
U4: L7805; TO-220-3_Vertical
U5: Buck_Converter; Buck Converter

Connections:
+3.3V: J5.4, U1.J2-1 (3V3), U2.2 (MS1), U2.3 (MS2), U2.4 (MS3)
+5V: U1.J2-19 (EXT_5V), U2.10 (VDD), U4.3 (OUT)
+6V: J1.2, J2.2, J3.2, J4.2, U2.16 (VMOT), U5.4 (OUT+)
/1A: J6.4, U2.12 (1A)
/1B: J6.3, U2.11 (1B)
/2A: J6.2, U2.13 (2A)
/2B: J6.1, U2.14 (2B)
/VBAT: BT1.1 (+), U4.1 (IN), U5.1 (IN+)
GND: BT1.2 (-), J1.1, J2.1, J3.1, J4.1, J5.1, U1.J2-14 (GND1), U1.J3-1 (GND3), U1.J3-7 (GND2), U2.9 (GND), U2.15 (GND), U4.2 (GND), U5.2 (IN-), U5.3 (OUT-)
unnamed: J1.3, U1.J2-7 (IO32)
unnamed: J2.3, U1.J2-8 (IO33)
unnamed: J3.3, U1.J2-9 (IO25)
unnamed: J4.3, U1.J2-10 (IO26)
unnamed: J5.2, U1.J3-9 (IO18)
unnamed: J5.3, U1.J3-8 (IO19)
unnamed: U1.J2-13 (IO12), U2.5 (~RESET)
unnamed: U1.J2-12 (IO14), U2.7 (STEP)
unnamed: U1.J2-11 (IO27), U2.8 (DIR)

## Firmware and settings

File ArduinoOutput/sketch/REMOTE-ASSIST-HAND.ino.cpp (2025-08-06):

#include <Arduino.h>
#line 1 "C:\\Users\\golcz\\remote-assist-hand\\Code\\REMOTE-ASSIST-HAND\\REMOTE-ASSIST-HAND.ino"
#include <WiFi.h>
#include <ESPAsyncWebServer.h>
#include <AsyncTCP.h>
#include <ArduinoJson.h>
#include <AccelStepper.h>
#include <ESP32Servo.h>
#include <ESP32PWM.h>
#include <Preferences.h>
#include "HX711.h"
#include "main_page.h"

// Wi-Fi creds
const char* ssid     = "FatCat";
const char* password = "snip1234";

// server + WS
AsyncWebServer server(80);
AsyncWebSocket  ws("/ws");

// pins
#define STEPPER_STEP_PIN 14
#define STEPPER_DIR_PIN  27
#define STEPPER_RST_PIN  12
#define SHOULDER_PIN     32
#define ELBOW_PIN        33
#define WRIST_PIN        25
#define GRASPER_PIN      26
#define HX711_DT_PIN     18
#define HX711_SCK_PIN    19

// motion params
const float STEPPER_MAX_SPEED    = 800.0;
const float STEPPER_ACCELERATION = 200.0;
const float SERVO_SMOOTHING      = 0.05;   // 0=no filter, 1=instant
const float SERVO_MOVE_SPEED     = 60.0;   // deg/sec when held

// safe motion limits (degrees)
const float SHOULDER_MIN_ANG = 30.0;
const float SHOULDER_MAX_ANG = 150.0;
const float ELBOW_MIN_ANG    = 0.0;
const float ELBOW_MAX_ANG    = 135.0;
const float WRIST_MIN_ANG    = 10.0;
const float WRIST_MAX_ANG    = 160.0;
const float GRASPER_MIN_ANG  = 20.0;
const float GRASPER_MAX_ANG  = 100.0;

// force sensor
float       FORCE_CALIBRATION    = 1.0;
const unsigned long FORCE_INTERVAL = 200;

// drift & filter state
static float lastForce       = 0.0;
static long  runningOffset   = 0;
static bool  offsetInited    = false;
unsigned long lastDriftTime  = 0;

// hardware
AccelStepper baseStepper(AccelStepper::DRIVER, STEPPER_STEP_PIN, STEPPER_DIR_PIN);
Servo        shoulder, elbow, wrist, grasper;
HX711        scale;
Preferences  prefs;

// angles & targets
float shoulderAngle, targetShoulderAngle;
float elbowAngle,    targetElbowAngle;
float wristAngle,    targetWristAngle;
float grasperAngle,  targetGrasperAngle;

// velocities (deg/sec)
float shoulderSpeed = 0, elbowSpeed = 0, wristSpeed = 0, grasperSpeed = 0;

//––– smoothing + pulse write with per-servo limits –––––––––––––––––––––––––
#line 73 "C:\\Users\\golcz\\remote-assist-hand\\Code\\REMOTE-ASSIST-HAND\\REMOTE-ASSIST-HAND.ino"
void updateServo(Servo &servo, float &cur, float tgt, float minA, float maxA);
#line 81 "C:\\Users\\golcz\\remote-assist-hand\\Code\\REMOTE-ASSIST-HAND\\REMOTE-ASSIST-HAND.ino"
void handleMotorCommand(const String &motor, const String &dir);
#line 93 "C:\\Users\\golcz\\remote-assist-hand\\Code\\REMOTE-ASSIST-HAND\\REMOTE-ASSIST-HAND.ino"
void handleMotorStop(const String &motor);
#line 117 "C:\\Users\\golcz\\remote-assist-hand\\Code\\REMOTE-ASSIST-HAND\\REMOTE-ASSIST-HAND.ino"
void onWebSocketEvent(AsyncWebSocket *s, AsyncWebSocketClient *c, AwsEventType type, void *arg, uint8_t *data, size_t len);
#line 139 "C:\\Users\\golcz\\remote-assist-hand\\Code\\REMOTE-ASSIST-HAND\\REMOTE-ASSIST-HAND.ino"
void stepperTask(void*);
#line 144 "C:\\Users\\golcz\\remote-assist-hand\\Code\\REMOTE-ASSIST-HAND\\REMOTE-ASSIST-HAND.ino"
void servoTask(void*);
#line 168 "C:\\Users\\golcz\\remote-assist-hand\\Code\\REMOTE-ASSIST-HAND\\REMOTE-ASSIST-HAND.ino"
void updateOffset();
#line 174 "C:\\Users\\golcz\\remote-assist-hand\\Code\\REMOTE-ASSIST-HAND\\REMOTE-ASSIST-HAND.ino"
float getFilteredForce();
#line 183 "C:\\Users\\golcz\\remote-assist-hand\\Code\\REMOTE-ASSIST-HAND\\REMOTE-ASSIST-HAND.ino"
void forceTask(void*);
#line 217 "C:\\Users\\golcz\\remote-assist-hand\\Code\\REMOTE-ASSIST-HAND\\REMOTE-ASSIST-HAND.ino"
void setup();
#line 281 "C:\\Users\\golcz\\remote-assist-hand\\Code\\REMOTE-ASSIST-HAND\\REMOTE-ASSIST-HAND.ino"
void loop();
#line 73 "C:\\Users\\golcz\\remote-assist-hand\\Code\\REMOTE-ASSIST-HAND\\REMOTE-ASSIST-HAND.ino"
void updateServo(Servo &servo, float &cur, float tgt, float minA, float maxA) {
  cur += (tgt - cur) * SERVO_SMOOTHING;
  float a = constrain(cur, minA, maxA);
  int us = map((int)a, (int)minA, (int)maxA, 500, 2500);
  servo.writeMicroseconds(us);
}

//––– WebSocket command handlers –––––––––––––––––––––––––––––––––––––––––
void handleMotorCommand(const String &motor, const String &dir) {
  if (motor == "base_stepper") {
    baseStepper.setSpeed(dir=="cw"? +STEPPER_MAX_SPEED : -STEPPER_MAX_SPEED);
    return;
  }
  float v = (dir=="cw"? +SERVO_MOVE_SPEED : -SERVO_MOVE_SPEED);
  if      (motor=="shoulder_servo") shoulderSpeed = v;
  else if (motor=="elbow_servo")    elbowSpeed    = v;
  else if (motor=="wrist_servo")    wristSpeed    = v;
  else if (motor=="grasper_servo")  grasperSpeed  = v;
}

void handleMotorStop(const String &motor) {
  if (motor == "base_stepper") {
    baseStepper.setSpeed(0);
    return;
  }
  if (motor=="shoulder_servo") {
    shoulderSpeed = 0;
    targetShoulderAngle = shoulderAngle;
    prefs.putFloat("shAng", shoulderAngle);
  } else if (motor=="elbow_servo") {
    elbowSpeed = 0;
    targetElbowAngle = elbowAngle;
    prefs.putFloat("elAng", elbowAngle);
  } else if (motor=="wrist_servo") {
    wristSpeed = 0;
    targetWristAngle = wristAngle;
    prefs.putFloat("wrAng", wristAngle);
  } else if (motor=="grasper_servo") {
    grasperSpeed = 0;
    targetGrasperAngle = grasperAngle;
    prefs.putFloat("grAng", grasperAngle);
  }
}

void onWebSocketEvent(AsyncWebSocket *s, AsyncWebSocketClient *c,
                      AwsEventType type, void *arg,
                      uint8_t *data, size_t len) {
  if (type == WS_EVT_CONNECT) {
    Serial.printf("[WS] Client %u connected\n", c->id());
  }
  else if (type == WS_EVT_DISCONNECT) {
    Serial.printf("[WS] Client %u disconnected\n", c->id());
  }
  else if (type == WS_EVT_DATA) {
    AwsFrameInfo *info = (AwsFrameInfo*)arg;
    if (!info->final || info->opcode!=WS_TEXT) return;
    String msg((char*)data, len);
    StaticJsonDocument<256> doc;
    if (deserializeJson(doc, msg)) return;
    String t = doc["type"], m = doc["motor"], dir = doc["dir"];
    if (t=="move")      handleMotorCommand(m, dir);
    else                  handleMotorStop(m);
  }
}

//––– stepper runner on core 0 –––––––––––––––––––––––––––––––––––––––
void stepperTask(void*) {
  for(;;) baseStepper.runSpeed();
}

//––– servo velocity + smoothing @50Hz on core 0 –––––––––––––––––––
void servoTask(void*) {
  const TickType_t period = pdMS_TO_TICKS(20);
  TickType_t lastWake = xTaskGetTickCount();
  const float dt = 20.0f/1000.0f;
  for (;;) {
    targetShoulderAngle = constrain(targetShoulderAngle + shoulderSpeed*dt,
                                    SHOULDER_MIN_ANG, SHOULDER_MAX_ANG);
    targetElbowAngle    = constrain(targetElbowAngle    + elbowSpeed*dt,
                                    ELBOW_MIN_ANG,    ELBOW_MAX_ANG);
    targetWristAngle    = constrain(targetWristAngle    + wristSpeed*dt,
                                    WRIST_MIN_ANG,    WRIST_MAX_ANG);
    targetGrasperAngle  = constrain(targetGrasperAngle  + grasperSpeed*dt,
                                    GRASPER_MIN_ANG,  GRASPER_MAX_ANG);

    updateServo(shoulder, shoulderAngle,       targetShoulderAngle, SHOULDER_MIN_ANG, SHOULDER_MAX_ANG);
    updateServo(elbow,    elbowAngle,          targetElbowAngle,    ELBOW_MIN_ANG,    ELBOW_MAX_ANG);
    updateServo(wrist,    wristAngle,          targetWristAngle,    WRIST_MIN_ANG,    WRIST_MAX_ANG);
    updateServo(grasper,  grasperAngle,        targetGrasperAngle,  GRASPER_MIN_ANG,  GRASPER_MAX_ANG);

    vTaskDelayUntil(&lastWake, period);
  }
}

//––– HX711 helpers –––––––––––––––––––––––––––––––––––––––––––––––––
void updateOffset(){
  long raw = scale.read_average(5);
  runningOffset = runningOffset*(1 - 0.01) + raw*0.01;
  scale.set_offset(runningOffset);
}

float getFilteredForce(){
  float units = scale.get_units(10);
  float filt  = lastForce*(1 - 0.2f) + units*0.2f;
  lastForce    = filt;
  if (fabs(filt) < 0.05f) filt = 0.0f;
  return filt * FORCE_CALIBRATION;
}

//––– force-streaming on core 1 –––––––––––––––––––––––––––––––––
void forceTask(void*) {
  const TickType_t period = pdMS_TO_TICKS(FORCE_INTERVAL);
  TickType_t lastWake = xTaskGetTickCount();
  int aliveCounter = 0;

  for (;;) {
    if (millis() - lastDriftTime > 5000) {
      updateOffset();
      lastDriftTime = millis();
    }

    float force = getFilteredForce();
    StaticJsonDocument<128> doc;
    doc["type"]  = "force";
    doc["motor"] = "grasper_servo";
    doc["force"] = force;
    String out; serializeJson(doc, out);
    ws.textAll(out);

    if (++aliveCounter >= 50) {
      StaticJsonDocument<64> hb;
      hb["type"]  = "heartbeat";
      hb["force"] = force;
      String j;
      serializeJson(hb, j);  // ← fixed: doc then dest
      ws.textAll(j);
      ws.pingAll();
      aliveCounter = 0;
    }

    vTaskDelayUntil(&lastWake, period);
  }
}

void setup() {
  Serial.begin(115200);
  pinMode(STEPPER_RST_PIN, OUTPUT);
  digitalWrite(STEPPER_RST_PIN, HIGH);
  delay(100);

  baseStepper.setMaxSpeed(STEPPER_MAX_SPEED);
  baseStepper.setAcceleration(STEPPER_ACCELERATION);

  shoulder.attach(SHOULDER_PIN, 500, 2500);
  elbow.attach(ELBOW_PIN,       500, 2500);
  wrist.attach(WRIST_PIN,       500, 2500);
  grasper.attach(GRASPER_PIN,   500, 2500);

  prefs.begin("servo", false);
  // load last or default to midpoint
  targetShoulderAngle = prefs.getFloat("shAng", (SHOULDER_MIN_ANG+SHOULDER_MAX_ANG)/2);
  shoulderAngle       = targetShoulderAngle;
  shoulder.writeMicroseconds(map((int)shoulderAngle, SHOULDER_MIN_ANG, SHOULDER_MAX_ANG, 500, 2500));

  targetElbowAngle = prefs.getFloat("elAng", (ELBOW_MIN_ANG+ELBOW_MAX_ANG)/2);
  elbowAngle       = targetElbowAngle;
  elbow.writeMicroseconds(map((int)elbowAngle, ELBOW_MIN_ANG, ELBOW_MAX_ANG, 500, 2500));

  targetWristAngle = prefs.getFloat("wrAng", (WRIST_MIN_ANG+WRIST_MAX_ANG)/2);
  wristAngle       = targetWristAngle;
  wrist.writeMicroseconds(map((int)wristAngle, WRIST_MIN_ANG, WRIST_MAX_ANG, 500, 2500));

  targetGrasperAngle = prefs.getFloat("grAng", (GRASPER_MIN_ANG+GRASPER_MAX_ANG)/2);
  grasperAngle       = targetGrasperAngle;
  grasper.writeMicroseconds(map((int)grasperAngle, GRASPER_MIN_ANG, GRASPER_MAX_ANG, 500, 2500));

  // Wi-Fi + server
  WiFi.mode(WIFI_STA);
  WiFi.begin(ssid, password);
  while (WiFi.status() != WL_CONNECTED) delay(500);

  server.on("/", HTTP_GET, [](AsyncWebServerRequest *r){
    r->send_P(200, "text/html", MAIN_PAGE);
  });
  server.on("/favicon.ico", HTTP_GET, [](AsyncWebServerRequest *r){ r->send(204); });
  ws.onEvent(onWebSocketEvent);
  server.addHandler(&ws);
  server.begin();

  // HX711 startup tare
  scale.begin(HX711_DT_PIN, HX711_SCK_PIN);
  scale.set_scale(FORCE_CALIBRATION);
  delay(500);
  long sum = 0;
  for (int i = 0; i < 50; i++) {
    sum += scale.read();
    delay(20);
  }
  runningOffset  = sum / 50;
  scale.set_offset(runningOffset);
  lastDriftTime  = millis();

  // tasks
  xTaskCreatePinnedToCore(stepperTask, "stepper", 1000, nullptr, 0, nullptr, 0);
  xTaskCreatePinnedToCore(servoTask,   "servo",   2048, nullptr, 1, nullptr, 0);
  xTaskCreatePinnedToCore(forceTask,   "force",   2048, nullptr, 1, nullptr, 1);
}

void loop() {
  delay(1000);
}

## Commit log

2025-05-28 Created the JOURNAL.md
    Created the JOURNAL.md file to journal the progress of brainstorming, designing and building the robotic arm.
2025-06-04 Updated MATERIALS-AND-BUDGET
2025-06-05 Updated MATERIALS-AND-BUDGET.md
2025-06-09 Updated MATERIALS-AND-BUDGET.md (June 9)
2025-06-09 Updated MATERIALS-AND-BUDGET.md Prices (June 9)
2025-06-12 Updated MATERIALS-AND-BUDGET.md (June 12)
2025-06-21 Updated JOURNAL.md Added Production Files Added CAD Files (June 20)
    [Base Center.step, Base Leg.step, Claw Bottom.step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]
2025-06-21 Updated CAD founder (June 20)
2025-06-21 Updated PCB Folder (June 20)
    [Heptic Feedback Arm.kicad_pcb, Heptic Feedback Arm.kicad_sch]
2025-06-21 Updated README.md and PCB foulder (June 20)
    [Heptic Feedback Arm.kicad_pcb, Heptic Feedback Arm.kicad_sch]
2025-06-21 Update and rename Bill of Materials (BOM) - Лист1 (2).csv to Bill of Materials (BOM.).csv
    [Bill of Materials (BOM.).csv]
2025-06-21 Update and rename Bill of Materials (BOM.).csv to Bill of Materials (BOM).csv
    [Bill of Materials (BOM).csv]
2025-06-21 Updated File Names in PCB Folder (June 20)
    [Haptic Feedback Arm.kicad_pcb, Haptic Feedback Arm.kicad_sch]
2025-06-21 Update Bill of Materials (BOM).csv
    [Bill of Materials (BOM).csv]
2025-06-21 Update and rename Bill of Materials (BOM) - Лист1 (3).csv to Bill of Materials (BOM).csv
    [Bill of Materials (BOM).csv]
2025-06-25 Updated BOM.csv (June 25)
    [Bill of Materials (BOM).csv]
2025-07-11 Updated Code Folder (July 10)
    [partitions.csv]
